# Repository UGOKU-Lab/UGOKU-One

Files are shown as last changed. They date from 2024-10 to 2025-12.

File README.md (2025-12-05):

UGOKU One のハードウェア（KiCad）リポジトリです。

[UGOKU One WEBサイト](https://ugoku-lab.github.io/ugokuone.html)

UGOKU One はモータやセンサを使ったロボットなどのDIY製作物を少しでも手軽に操作することを目的に開発しているオープンソースハードウェアの汎用基板です。
    
- 単四電池ボックス搭載で単四電池4本でDCモーターやRCサーボをの駆動が可能
- Arduinoで開発可能なESP32マイコン搭載(無線通信対応)
- DCモータドライバ（TB67H450FNG）を2個搭載
- 豊富な汎用IOポートでいろんな拡張が可能
- 圧着工具を使用せずにモーターやセンサーの配線が可能

現時点では開発中で動作は未保証です。





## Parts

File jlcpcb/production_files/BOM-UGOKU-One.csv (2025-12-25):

Comment | Designator | Footprint | LCSC | Quantity
0.1μF | C1,C13,C14,C2,C3,C4,C5,C7,C8 | C_0402_1005Metric | C307331 | 9
1.5k | R16,R17,R18,R7 | R_0603_1608Metric | C22843 | 4
10k | R1,R10,R11,R12,R13,R14,R19,R20,R21,R22,R24,R3,R8,R9 | R_0402_1005Metric | C25744 | 14
10μF | C10,C15,C16 | C_0805_2012Metric | C440198 | 3
22.1k | R5 | R_0402_1005Metric | C25768 | 1
22μF | C11,C17,C18,C6,C9 | C_0805_2012Metric | C45783 | 5
47.5k | R6 | R_0402_1005Metric | C25792 | 1
470 | R15,R23 | R_0603_1608Metric | C23179 | 2
470μF | C12 | CP_Elec_6.3x7.7 | C709470 | 1
5.1k | R2,R4 | R_0402_1005Metric | C25905 | 2
AMS1117-3.3 | U3 | SOT-223-3_TabPin2 | C6186 | 1
BMI270 | U4 | XDCR_BMI270 | C2836813 | 1
Battery | BT1 | BAT_2481 | C7174242 | 1
CP2102N-A02-GQFN28 | U1 | IC_CP2102N-A02-GQFN28R | C964632 | 1
Conn_01x02 | J10,J11,J12,J2 | PTS_1.5_2 | C3032345 | 4
Conn_01x10 | J4 | PinSocket_1x10_P2.54mm_Vertical | C2897373 | 1
Conn_02x03_Odd_Even | J3,J8,J9 | PinHeader_2x03_P2.54mm_Vertical_SMD | C3294461 | 3
ESP32-WROOM-32E | U5 | ESP32-WROOM-32E | C701342 | 1
Harting-Conn | J5,J6 | 14110513001000 | C5475480 | 2
K7805M/M78AR05 | U2 | M78AR | C2992391 | 1
LED | L2,L3,L4 | LED_0805_2012Metric_Pad1.15x1.40mm_HandSolder | C84256 | 3
LESD5D5.0CT1G | D1,D2,D3 | D_SOD-523 | C383211 | 3
PWR | L1 | LED_0805_2012Metric_Pad1.15x1.40mm_HandSolder | C434435 | 1
SMBJ6.5A | D7 | D_SMB | C41376096 | 1
SS54 | D4,D5,D6,D8 | D_SMA | C22452 | 4
SS8050 | Q1,Q2 | SOT-23 | C2150 | 2
SSM3K333R | Q3 | SOT-23F | C395454 | 1
SW_DIP_x02 | SW4 | SW_DIP_SPSTx02_Slide_Omron_A6S-210x_W8.9mm_P2.54mm | C6331180 | 1
SW_Push | SW2,SW3 | SW_Push_1P1T_NO_Vertical_Wuerth_434133025816 | C115360 | 2
SW_SPDT | SW1 | SW_SS-12M11G5 | C2879839 | 1
TB67H450FNG_EL | U6,U7 | HSOP-8-1EP_3.9x4.9mm_P1.27mm_EP2.3x2.3mm | C545417 | 2
USB_C_Receptacle_USB2.0_16P | J1 | USB_C_Receptacle_GCT_USB4105-xx-A_16P_TopMnt_Horizontal | C2765186 | 1
Conn_01x04 | J7 | PinHeader_1x04_P2.54mm_Vertical |  | 1

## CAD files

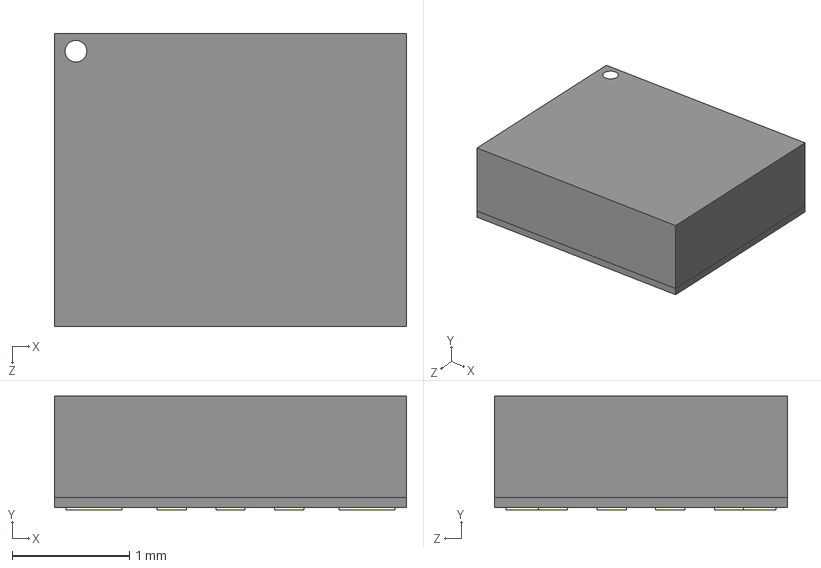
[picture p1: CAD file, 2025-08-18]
3Dmodels/ICM-42605.step
3.00 x 0.97 x 2.50 mm

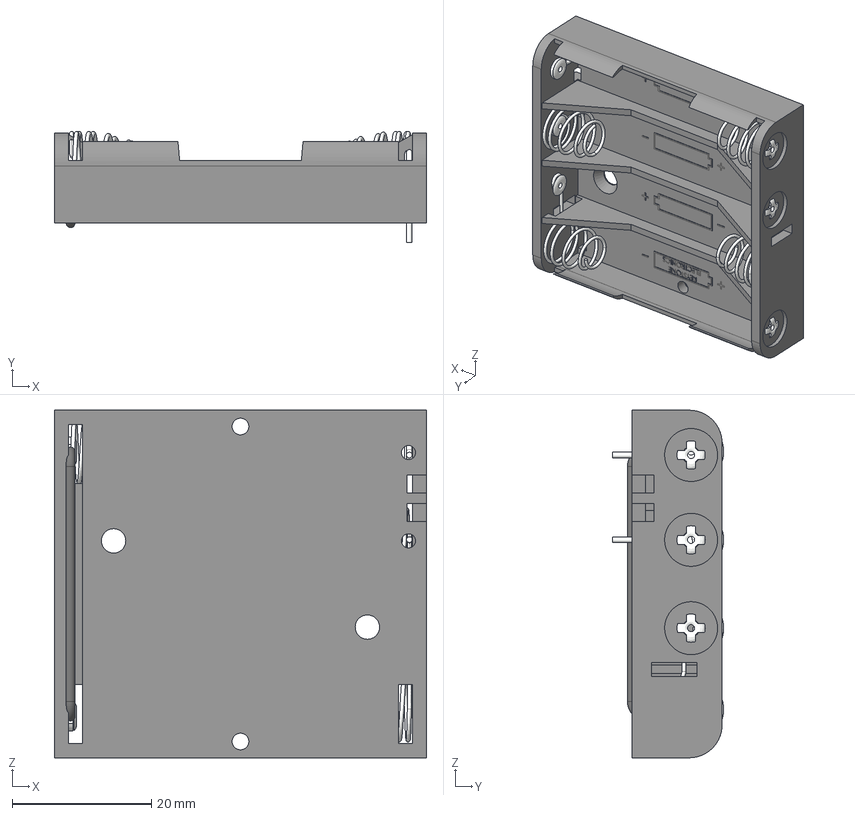
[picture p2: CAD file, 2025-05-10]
3Dmodels/2481_4xAAA_holder.STEP
53.5 x 16.0 x 50.0 mm

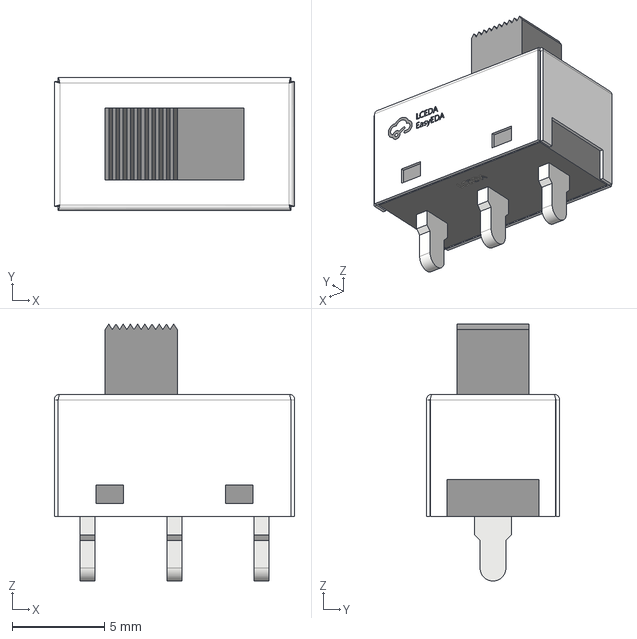
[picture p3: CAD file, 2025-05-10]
3Dmodels/SW_XKB_SS-12M11G5.step
13.0 x 7.20 x 13.9 mm

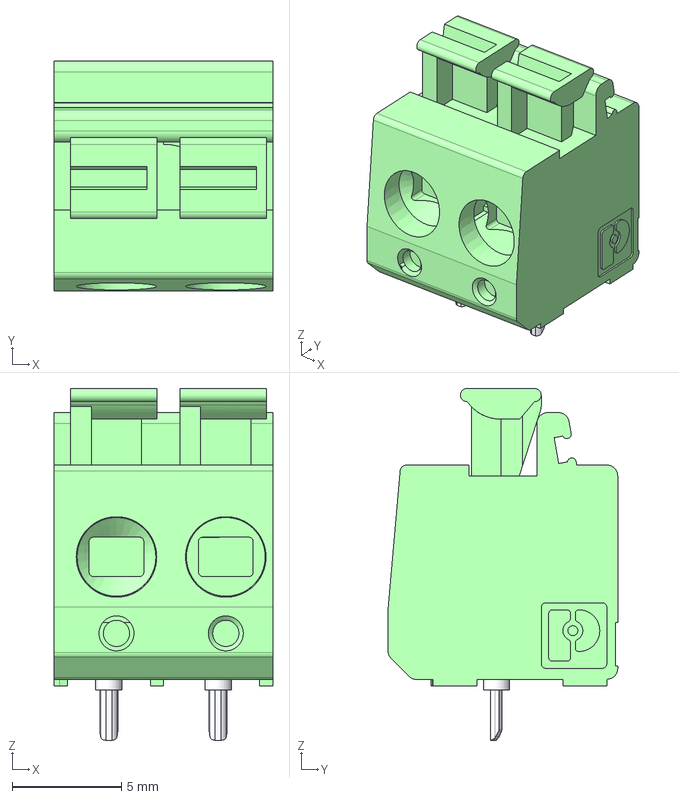
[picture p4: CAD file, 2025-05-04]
3Dmodels/PTS-1-5-2.stp
10.0 x 10.5 x 16.1 mm

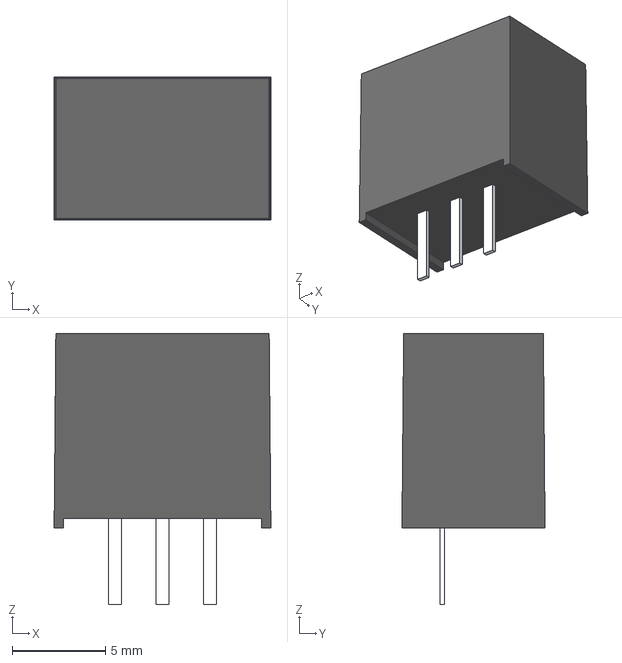
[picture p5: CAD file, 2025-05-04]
3Dmodels/M78AR-1.stp
11.6 x 7.66 x 14.5 mm

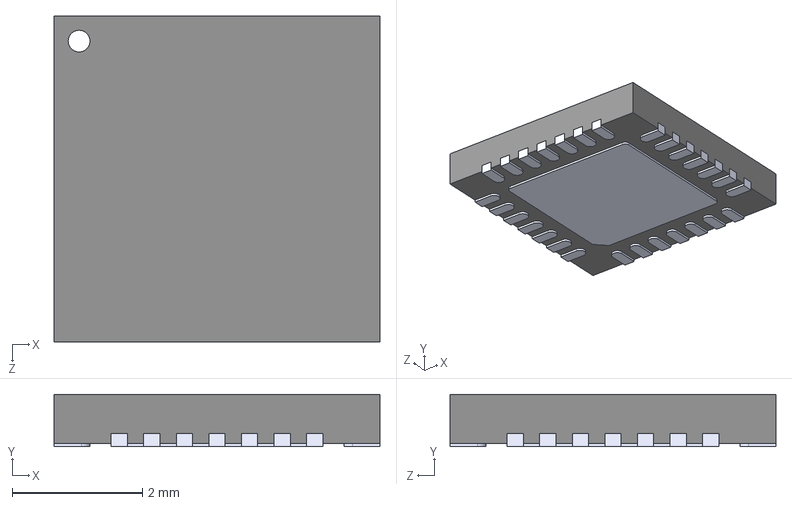
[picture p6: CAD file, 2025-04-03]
3Dmodels/CP2102N-A02-GQFN28R.step
5.00 x 0.8 x 5.00 mm

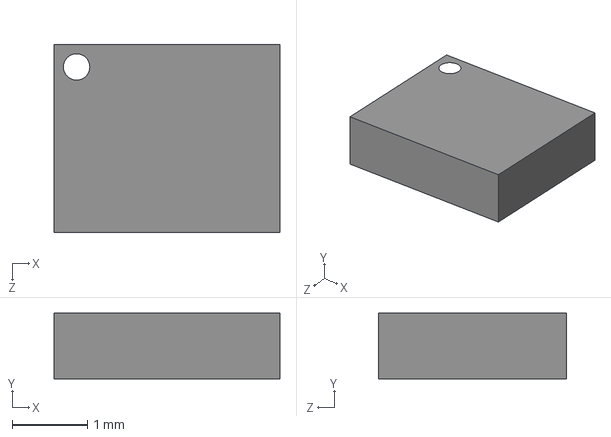
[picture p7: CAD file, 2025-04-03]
3Dmodels/BMI270.step
3.00 x 0.87 x 2.50 mm

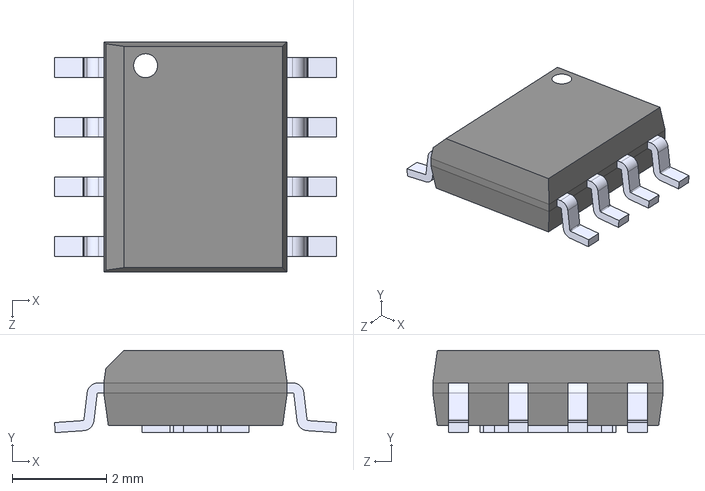
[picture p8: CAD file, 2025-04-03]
3Dmodels/TB67H450FNG.STEP
6.00 x 1.75 x 4.90 mm

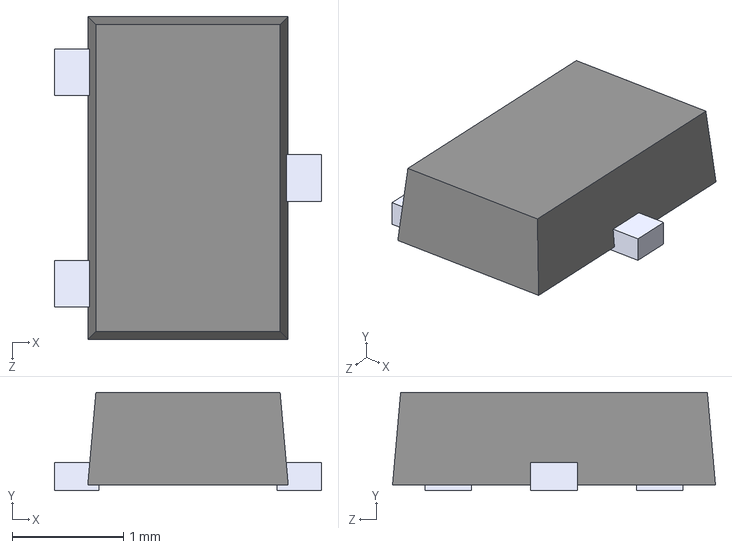
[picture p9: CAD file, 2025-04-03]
3Dmodels/SOT-23F.step
2.40 x 0.88 x 2.90 mm

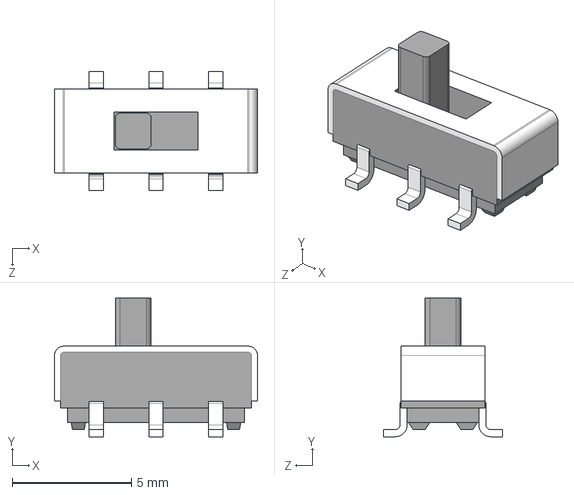
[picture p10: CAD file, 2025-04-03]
3Dmodels/SSSS213202.STEP
8.50 x 5.80 x 5.00 mm

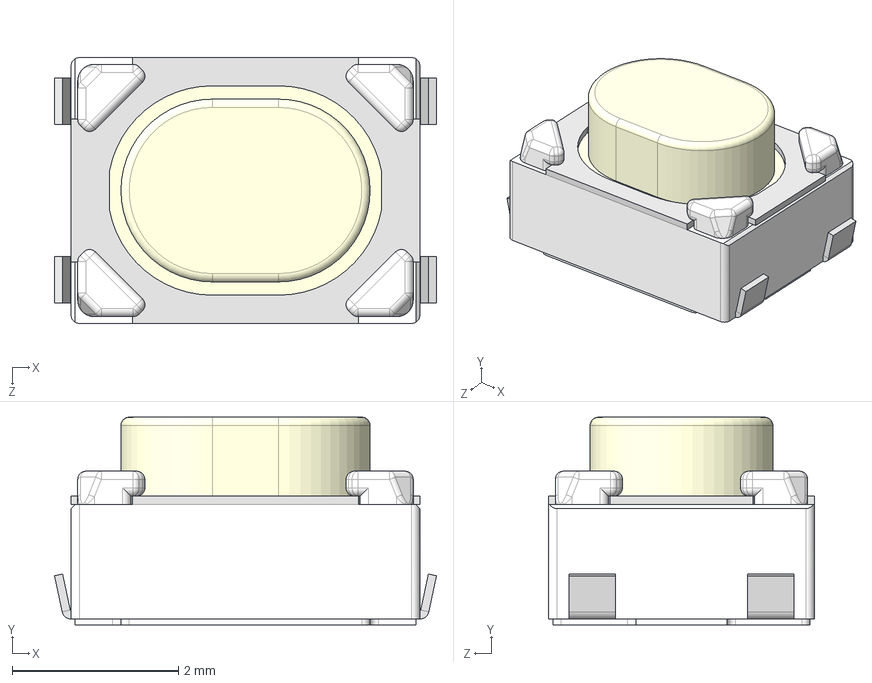
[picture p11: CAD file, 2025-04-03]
3Dmodels/SKRPAB.STEP
4.60 x 2.50 x 3.20 mm

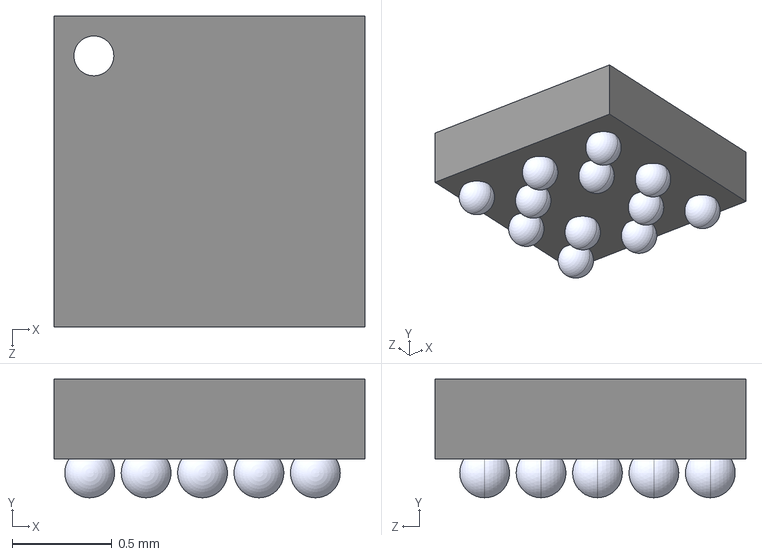
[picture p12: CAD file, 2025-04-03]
3Dmodels/BMM150.STEP
1.56 x 0.595 x 1.56 mm
Body^BMM150
Pin^BMM150 x 12

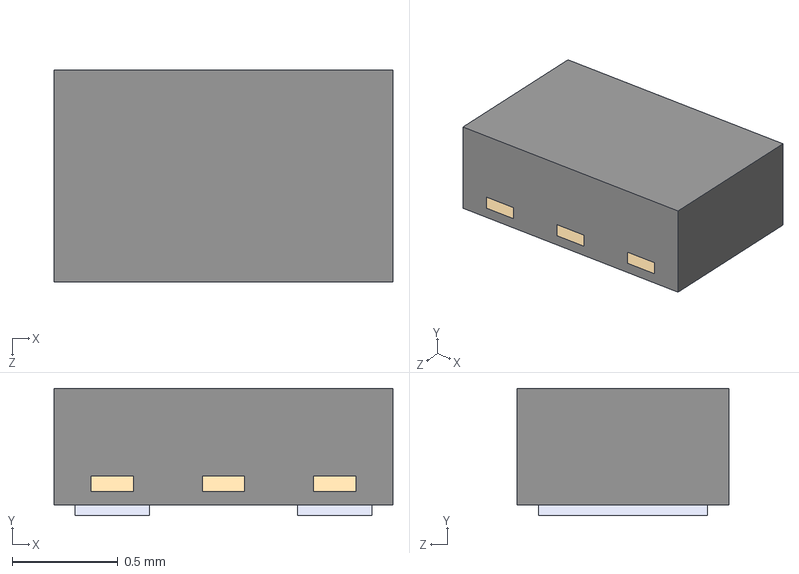
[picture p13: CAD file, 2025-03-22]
3Dmodels/ESDA25P35-1U1M.step
1.60 x 0.6 x 1.00 mm

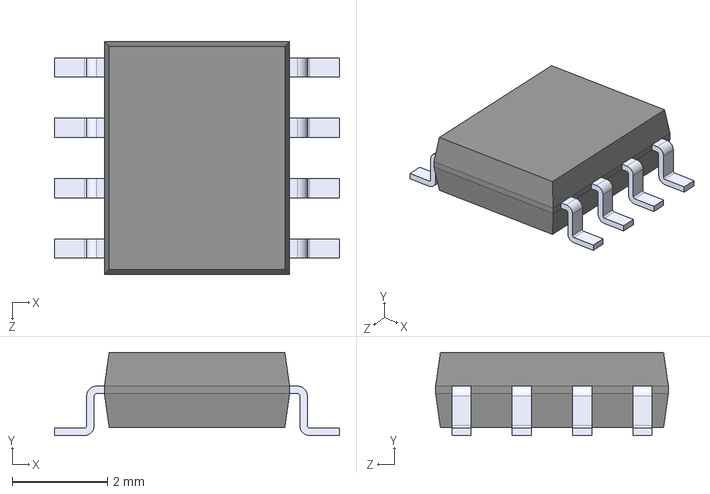
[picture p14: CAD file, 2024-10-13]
3Dmodels/MCP2562-E_SN.step
6.00 x 1.75 x 4.90 mm

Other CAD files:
3Dmodels/TL3301FF160QG.step
3Dmodels/14010213102000.stp
3Dmodels/14110513001000.stp
3Dmodels/14110413001000.stp
3Dmodels/14110213001000.stp
3Dmodels/14110313001000.stp

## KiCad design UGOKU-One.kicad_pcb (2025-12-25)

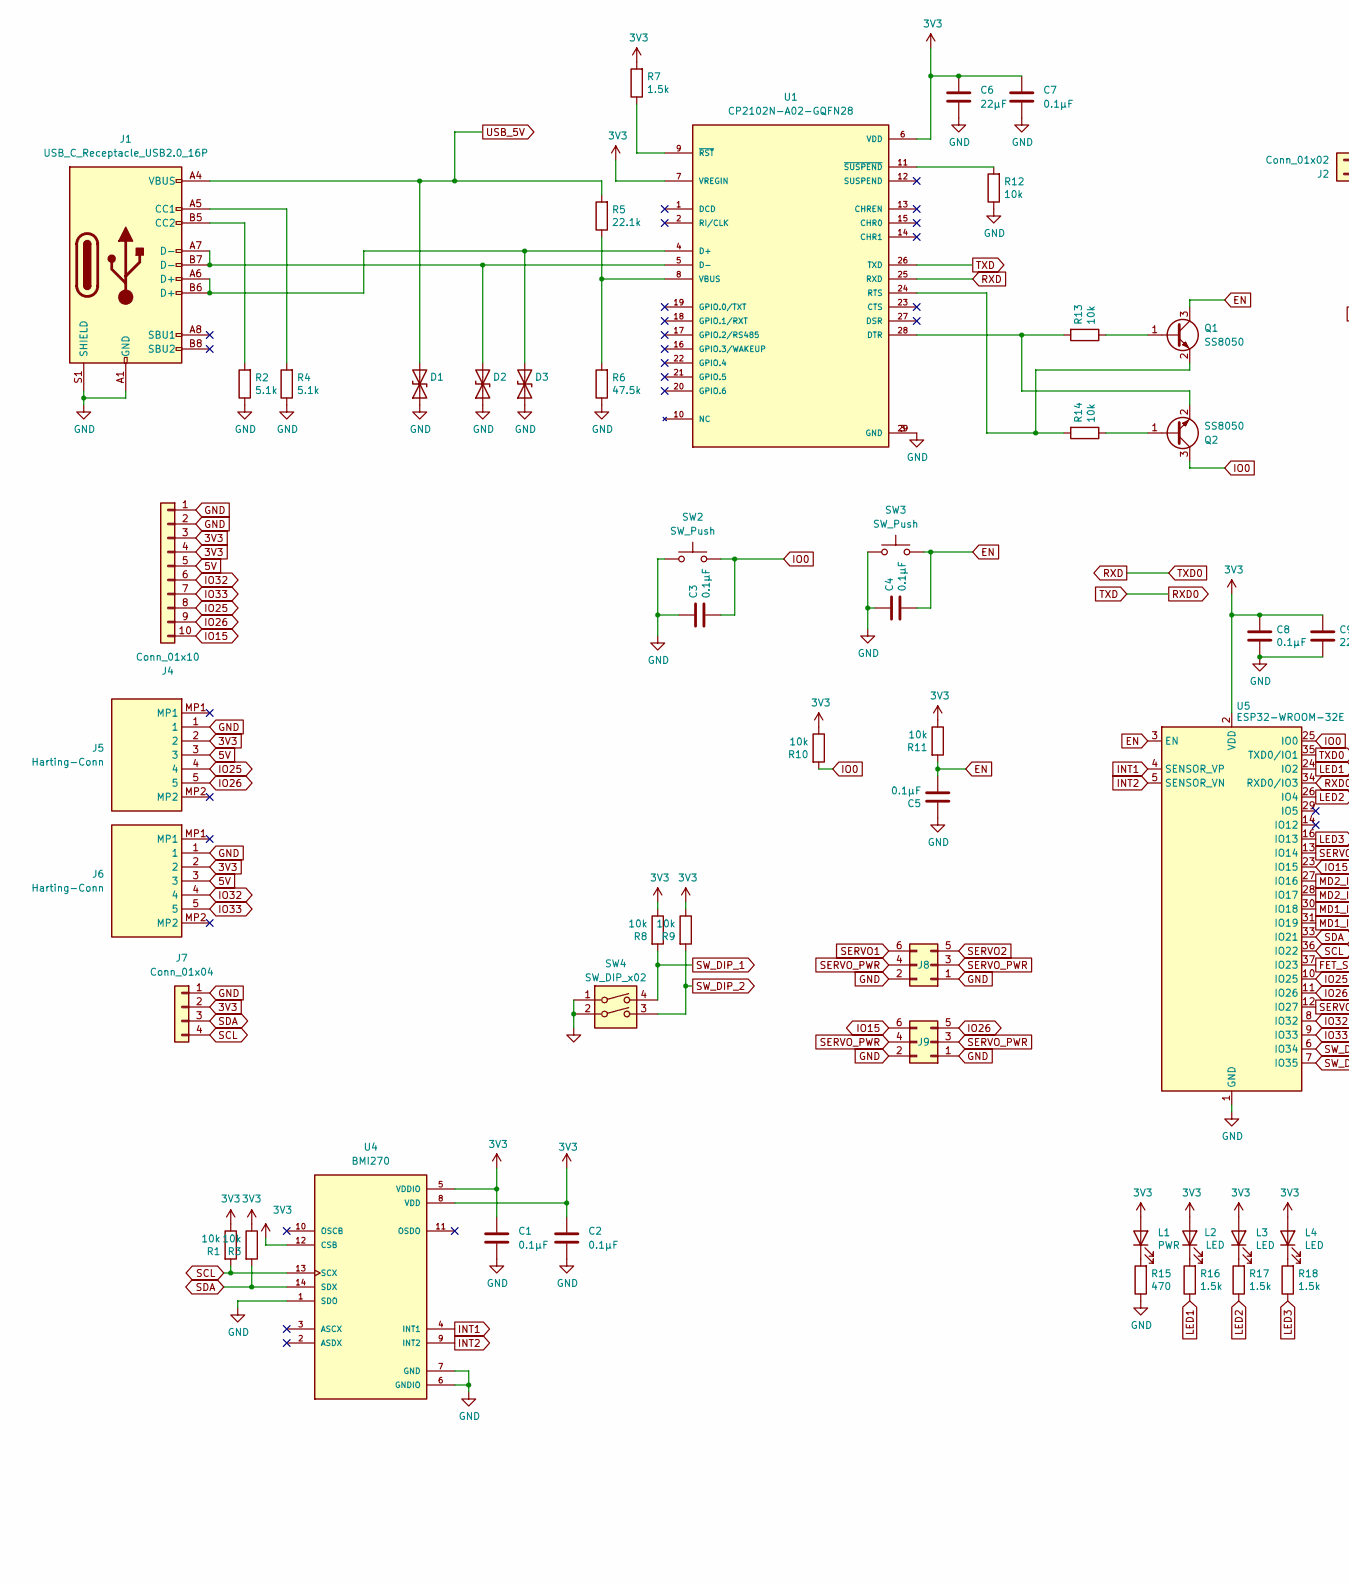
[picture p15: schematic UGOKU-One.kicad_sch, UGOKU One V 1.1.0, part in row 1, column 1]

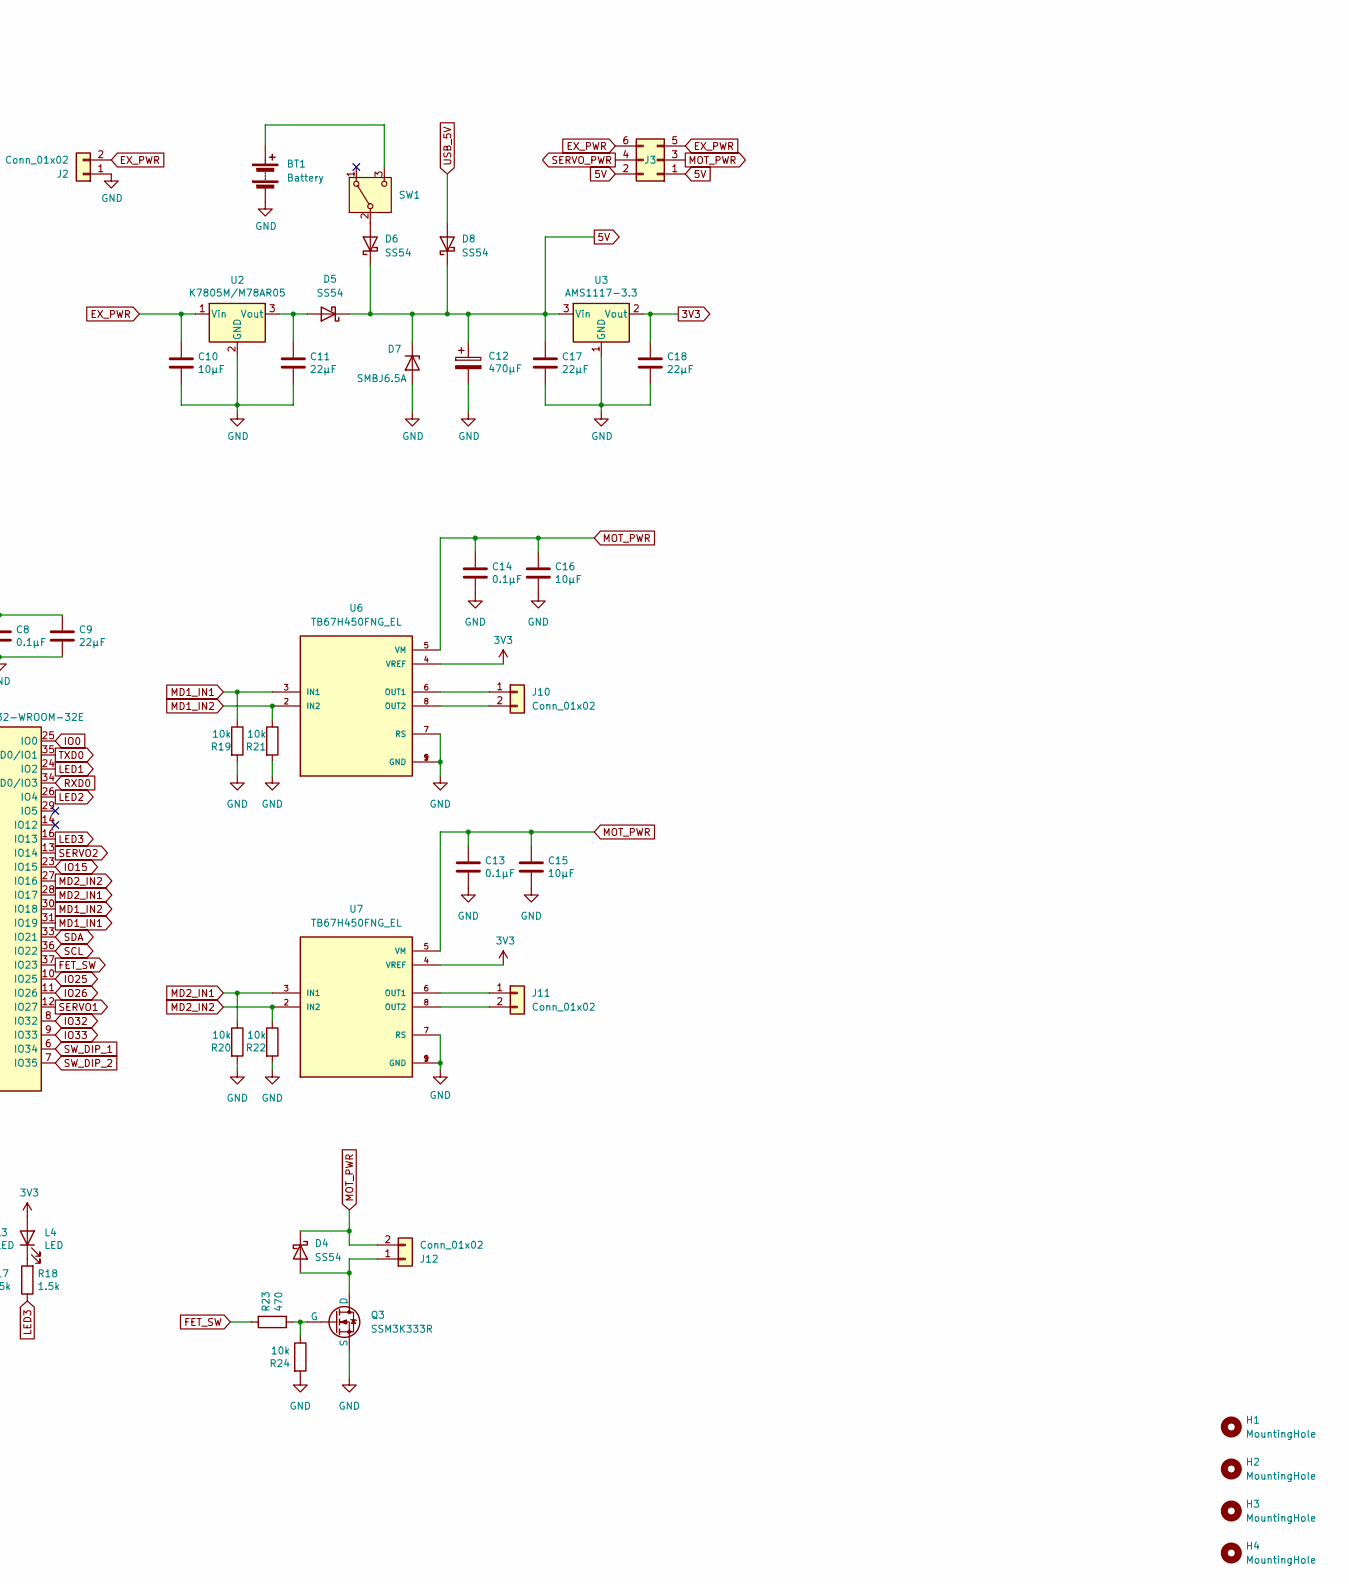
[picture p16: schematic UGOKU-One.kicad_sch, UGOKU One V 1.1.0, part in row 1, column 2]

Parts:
BT1: Battery; BAT_2481
C1, C2, C3, C4, C5, C7, C8, C13, C14: 0.1μF; C_0402_1005Metric
C6, C9, C11, C17, C18: 22μF; C_0805_2012Metric
C10, C15, C16: 10μF; C_0805_2012Metric
C12: 470μF; CP_Elec_6.3x7.7
D1, D2, D3: LESD5D5.0CT1G; D_SOD-523
D4, D5, D6, D8: SS54; D_SMA
D7: SMBJ6.5A; D_SMB
H1, H2, H3, H4: MountingHole; MountingHole_3.2mm_M3
J1: USB_C_Receptacle_USB2.0_16P; USB_C_Receptacle_GCT_USB4105-xx-A_16P_TopMnt_Horizontal
J2, J10, J11, J12: Conn_01x02; PTS_1.5_2
J3, J8, J9: Conn_02x03_Odd_Even; PinHeader_2x03_P2.54mm_Vertical_SMD
J4: Conn_01x10; PinSocket_1x10_P2.54mm_Vertical
J5, J6: Harting-Conn; 14110513001000; Manufacturer_Part_Number 14110513001000; Mouser Part Number 617-14110513001000
J7: Conn_01x04; PinHeader_1x04_P2.54mm_Vertical
L1: PWR; LED_0805_2012Metric_Pad1.15x1.40mm_HandSolder
L2, L3, L4: LED; LED_0805_2012Metric_Pad1.15x1.40mm_HandSolder
Q1, Q2: SS8050; SOT-23
Q3: SSM3K333R; SOT-23F
R1, R3, R8, R9, R10, R11, R12, R13, R14, R19, R20, R21, R22, R24: 10k; R_0402_1005Metric
R2, R4: 5.1k; R_0402_1005Metric
R5: 22.1k; R_0402_1005Metric
R6: 47.5k; R_0402_1005Metric
R7, R16, R17, R18: 1.5k; R_0603_1608Metric
R15, R23: 470; R_0603_1608Metric
SW1: SW_SPDT; SW_SS-12M11G5
SW2, SW3: SW_Push; SW_Push_1P1T_NO_Vertical_Wuerth_434133025816
SW4: SW_DIP_x02; SW_DIP_SPSTx02_Slide_Omron_A6S-210x_W8.9mm_P2.54mm
U1: CP2102N-A02-GQFN28; IC_CP2102N-A02-GQFN28R; PARTREV 1.5
U2: K7805M/M78AR05; M78AR
U3: AMS1117-3.3; SOT-223-3_TabPin2
U4: BMI270; XDCR_BMI270
U5: ESP32-WROOM-32E
U6, U7: TB67H450FNG_EL; HSOP-8-1EP_3.9x4.9mm_P1.27mm_EP2.3x2.3mm; PARTREV 3.0

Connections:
3V3: C1.1, C2.1, C6.1, C7.1, C8.1, C9.1, C18.1, J4.3, J4.4, J5.2, J6.2, J7.2, L1.2 (A), L2.2 (A), L3.2 (A), L4.2 (A), R1.1, R3.1, R7.2, R8.1, R9.1, R10.1, R11.1, U1.6 (VDD), U1.7 (VREGIN), U3.2 (Vout), U4.5 (VDDIO), U4.8 (VDD), U4.12 (CSB), U5.2 (VDD), U6.4 (VREF), U7.4 (VREF)
5V: C12.1, C17.1, D5.1 (K), D6.1 (K), D7.1 (K), D8.1 (K), J3.1, J3.2, J4.5, J5.3, J6.3, U3.3 (Vin)
EN: C4.2, C5.2, Q1.3 (C), R11.2, SW3.2, U5.3 (EN)
EX_PWR: C10.1, J2.2, J3.5, J3.6, U2.1 (Vin)
FET_SW: R23.2, U5.37 (IO23)
GND: BT1.2 (-), C1.2, C2.2, C3.1, C4.1, C5.1, C6.2, C7.2, C8.2, C9.2, C10.2, C11.2, C12.2, C13.2, C14.2, C15.2, C16.2, C17.2, C18.2, D1.1 (A1), D2.1 (A1), D3.1 (A1), D7.2 (A), J1.A1 (GND), J1.A12 (GND), J1.B1 (GND), J1.B12 (GND), J1.S1 (SHIELD), J2.1, J4.1, J4.2, J5.1, J6.1, J7.1, J8.1, J8.2, J9.1, J9.2, Q3.2 (S), R2.1, R4.1, R6.1, R12.1, R15.1, R19.2, R20.2, R21.2, R22.2, R24.2, SW2.1, SW3.1, SW4.1, SW4.2, U1.3 (GND), U1.29 (GND), U2.2 (GND), U3.1 (GND), U4.1 (SDO), U4.6 (GNDIO), U4.7 (GND), U5.1 (GND), U5.15 (GND), U5.38 (GND), U5.39 (GND), U6.1 (GND), U6.7 (RS), U6.9 (GND), U7.1 (GND), U7.7 (RS), U7.9 (GND)
INT1: U4.4 (INT1), U5.4 (SENSOR_VP)
INT2: U4.9 (INT2), U5.5 (SENSOR_VN)
IO0: C3.2, Q2.3 (C), R10.2, SW2.2, U5.25 (IO0)
IO15: J4.10, J9.6, U5.23 (IO15)
IO25: J4.8, J5.4, U5.10 (IO25)
IO26: J4.9, J5.5, J9.5, U5.11 (IO26)
IO32: J4.6, J6.4, U5.8 (IO32)
IO33: J4.7, J6.5, U5.9 (IO33)
LED1: R16.1, U5.24 (IO2)
LED2: R17.1, U5.26 (IO4)
LED3: R18.1, U5.16 (IO13)
MD1_IN1: R19.1, U5.31 (IO19), U6.3 (IN1)
MD1_IN2: R21.1, U5.30 (IO18), U6.2 (IN2)
MD2_IN1: R20.1, U5.28 (IO17), U7.3 (IN1)
MD2_IN2: R22.1, U5.27 (IO16), U7.2 (IN2)
MOT_PWR: C13.1, C14.1, C15.1, C16.1, D4.1 (K), J3.3, J12.2, U6.5 (VM), U7.5 (VM)
unnamed: BT1.1 (+), SW1.3 (C)
unnamed: D2.2 (A2), J1.A7 (D-), J1.B7 (D-), U1.5 (D-)
unnamed: D3.2 (A2), J1.A6 (D+), J1.B6 (D+), U1.4 (D+)
unnamed: D4.2 (A), J12.1, Q3.3 (D)
unnamed: C11.1, D5.2 (A), U2.3 (Vout)
unnamed: D6.2 (A), SW1.2 (B)
unnamed: J1.A5 (CC1), R4.2
unnamed: J1.B5 (CC2), R2.2
unnamed: J10.1, U6.6 (OUT1)
unnamed: J10.2, U6.8 (OUT2)
unnamed: J11.1, U7.6 (OUT1)
unnamed: J11.2, U7.8 (OUT2)
unnamed: L1.1 (K), R15.2
unnamed: L2.1 (K), R16.2
unnamed: L3.1 (K), R17.2
unnamed: L4.1 (K), R18.2
unnamed: Q1.1 (B), R13.1
unnamed: Q1.2 (E), R14.2, U1.24 (RTS)
unnamed: Q2.1 (B), R14.1
unnamed: Q2.2 (E), R13.2, U1.28 (DTR)
unnamed: Q3.1 (G), R23.1, R24.1
unnamed: R5.1, R6.2, U1.8 (VBUS)
unnamed: R7.1, U1.9 (~RST)
unnamed: R12.2, U1.11 (~SUSPEND)
RXD: U1.25 (RXD), U5.35 (TXD0/IO1)
RXD0: U1.26 (TXD), U5.34 (RXD0/IO3)
SCL: J7.4, R1.2, U4.13 (SCX), U5.36 (IO22)
SDA: J7.3, R3.2, U4.14 (SDX), U5.33 (IO21)
SERVO1: J8.6, U5.12 (IO27)
SERVO2: J8.5, U5.13 (IO14)
SERVO_PWR: J3.4, J8.3, J8.4, J9.3, J9.4
SW_DIP_1: R8.2, SW4.4, U5.6 (IO34)
SW_DIP_2: R9.2, SW4.3, U5.7 (IO35)
USB_5V: D1.2 (A2), D8.2 (A), J1.A4 (VBUS), J1.A9 (VBUS), J1.B4 (VBUS), J1.B9 (VBUS), R5.2

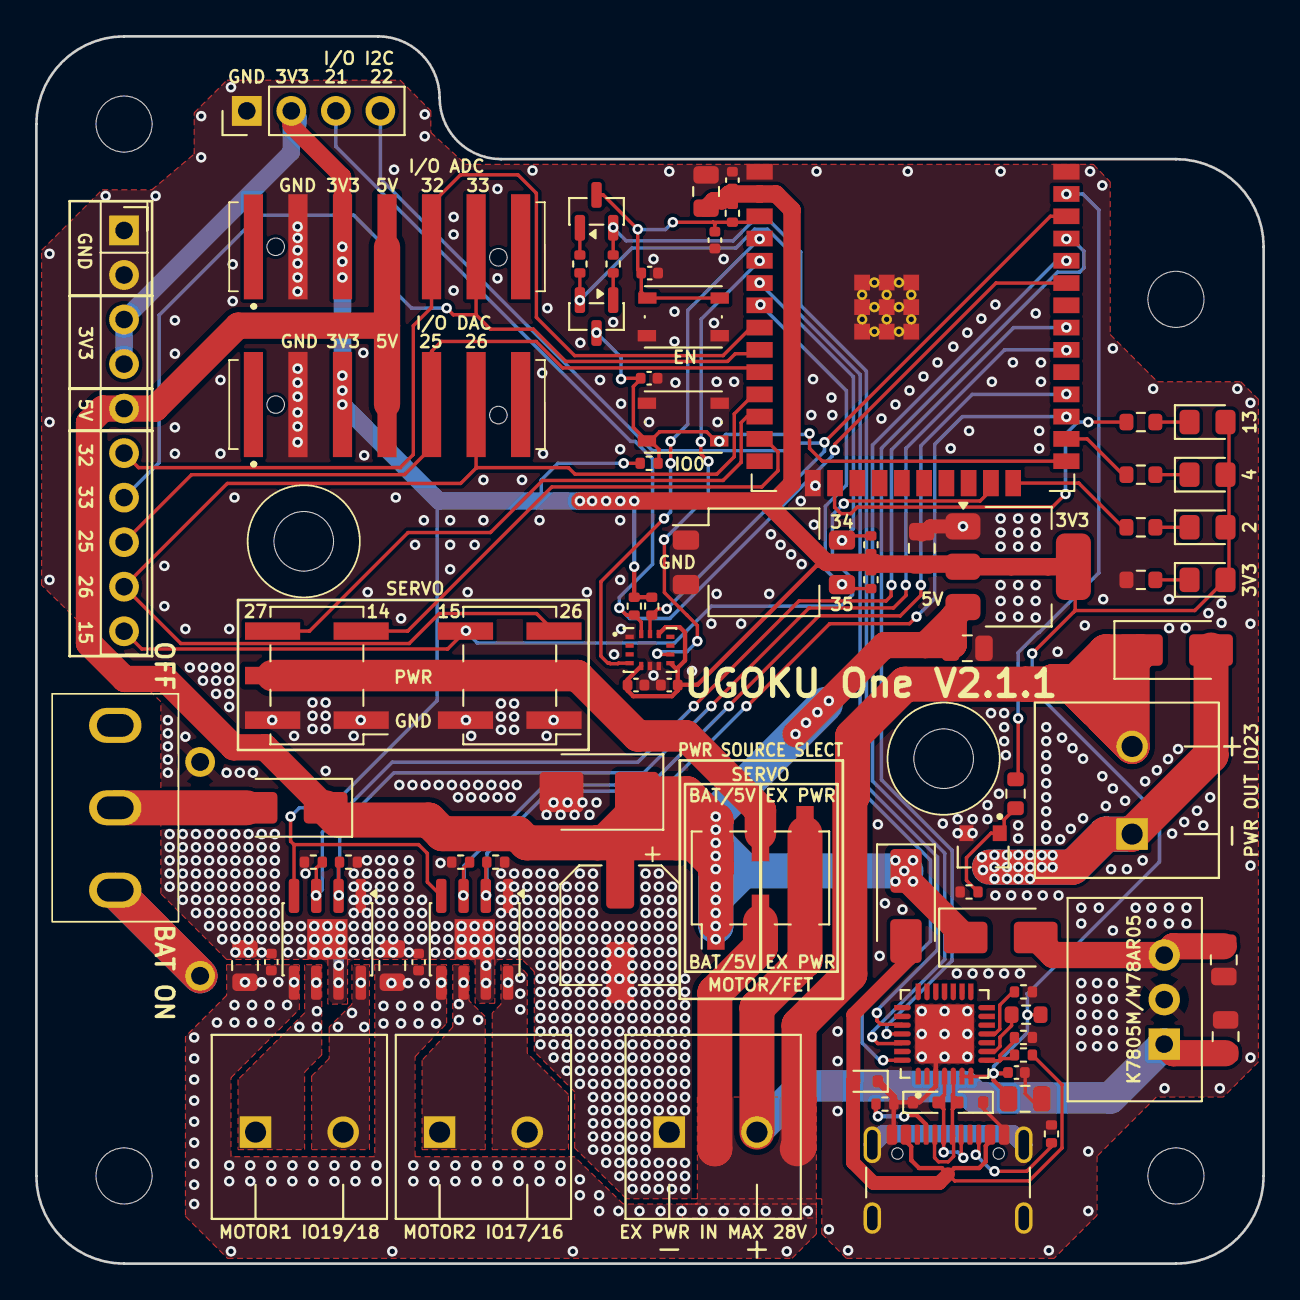
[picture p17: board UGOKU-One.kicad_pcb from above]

Board: 2 copper layers, 70.0 x 70.0 mm, 85 parts (1 on the bottom side), 56 nets.

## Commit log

2024-07-21 Hand over data from previous UGOKU-One (Now UGOKU-Pro)
    [UGOKU-One.kicad_pcb, UGOKU-One.kicad_sch]
2024-07-21 commit iroiro
    [UGOKU-One.kicad_pcb, UGOKU-One.kicad_sch]
2024-10-13 make concept
    [14110213001000.PcbLib, 14110213001000.SchLib, 14110213001000.psm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]
2025-03-17 modify usb, power
    [UGOKU-One.kicad_pcb, UGOKU-One.kicad_sch]
2025-03-22 add PD
    [ESDA25P35-1U1M.step, UGOKU-One.kicad_pcb, UGOKU-One.kicad_sch]
2025-03-28 V1 Rough Layout
    [UGOKU-One.kicad_pcb, UGOKU-One.kicad_sch]
2025-03-30 Add IMU, FET
    [14110213001000.PcbLib, 14110213001000.SchLib, 14110213001000.psm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]
2025-03-31 power layout draft
    [UGOKU-One.kicad_pcb, UGOKU-One.kicad_sch]
2025-03-31 Remove cached KiCad temporary files
2025-04-03 Power:near complete
    [14010213102000.stp, 14110513001000.stp, 2481_4xAAA_holder.STEP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]
2025-04-16 Almost done
    [UGOKU-One.kicad_pcb, UGOKU-One.kicad_sch]
2025-05-04 April-22 order spec
    [UGOKU-One.kicad_pcb, UGOKU-One.kicad_sch]
2025-05-04 update 3dmodel connector color
    [14010213102000.stp, 14110513001000.stp]
2025-05-04 update parts 3dmodel path
    [M78AR-1.stp, PTS-1-5-2.stp, UGOKU-One.kicad_pcb]
2025-05-04 update 3dmodel path
    [UGOKU-One.kicad_pcb]
2025-05-10 update 3dmodels
    [2481_4xAAA_holder.STEP, SW_XKB_SS-12M11G5.step, UGOKU-One.kicad_pcb]
2025-05-16 correct TXRX, regulator pin assign add batt thermal pad
    [UGOKU-One.kicad_pcb, UGOKU-One.kicad_sch]
2025-05-18 align resistor
    [UGOKU-One.kicad_pcb]
2025-06-11 add Motor Drive IN1/2 PIN PullDown, IO0 PIN PullUp
    [UGOKU-One.kicad_pcb, UGOKU-One.kicad_sch]
2025-06-11 Add Title to sch, Update sch pdf
    [UGOKU-One.kicad_sch]
2025-06-14 JLCPCBの要求に対応するため最小viaサイズを0.3/0.5に変更、JLCPCBの要求に対応するためvia-Padクリアランス確保のため地磁気センサBMM150を廃止、スイッチング出力用FETのピン配置を修正
    [UGOKU-One.kicad_pcb, UGOKU-One.kicad_sch]
2025-06-14 IMUの待機電力が微小のため、IMUの電源スイッチを廃止
    [UGOKU-One.kicad_pcb, UGOKU-One.kicad_sch]
2025-08-15 電池ボックスボルトをM2.6に変更 JLCPCB tool 部品表の部品座標、向きを修正
    [UGOKU-One.kicad_pcb]
2025-08-15 CPLファイルの座標と向きを修正、電池ボックスねじ締結指示の画像を追加
    [BOM-UGOKU-One.csv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]
2025-08-18 add part lib
    [ICM-42605.step]
2025-08-23 JLCPCB economy に対応するためIMUをICM-42605に変更
    [UGOKU-One.kicad_pcb]
2025-08-24 ピン配置とコネクタ配置を変更
    [BOM-UGOKU-One.csv, UGOKU-One.kicad_pcb, UGOKU-One.kicad_sch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]
2025-08-31 Update README for ESP32 microcontroller description
2025-10-26 5V電源でアクチュエータを駆動する際の安定性および安全性向上のためにのためにTVSダイオードと電解コンデンサを追加 PCB上に配置（未配線）
    [BOM-UGOKU-One.csv, UGOKU-One.kicad_pcb, UGOKU-One.kicad_sch]
2025-11-22 TVSダイオードをSMBJ6.0に変更
    [BOM-UGOKU-One.csv, UGOKU-One.kicad_pcb, UGOKU-One.kicad_sch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]
2025-12-04 5VラインのコンデンサとTVSダイオードの配線を実施 IMUをBMI270に戻し
    [BOM-UGOKU-One.csv, UGOKU-One.kicad_pcb, UGOKU-One.kicad_sch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]
2025-12-05 配線、ビア、シルクスクリーンの修正
    [UGOKU-One.kicad_pcb]
2025-12-05 ベタGNDとviaを修正
    [UGOKU-One.kicad_pcb, UGOKU-One.kicad_sch]
2025-12-05 ベタGNDを修正
    [UGOKU-One.kicad_pcb]
2025-12-06 MD周りのベタ, viaを修正 BOM,CPLファイルを整備
    [BOM-UGOKU-One.csv, UGOKU-One.kicad_pcb, UGOKU-One.kicad_sch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]
2025-12-06 最新の修正を反映
2025-12-07 ビアの位置を修正
    [UGOKU-One.kicad_pcb]
2025-12-07 製造用CPLファイルの電池ボックスの位置を修正
    [CPL-UGOKU-One.csv]
2025-12-07 コスト削減のため抵抗の種類を統一
    [BOM-UGOKU-One.csv, UGOKU-One.kicad_pcb, UGOKU-One.kicad_sch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]
2025-12-08 抵抗の種類削減
    [UGOKU-One.kicad_pcb, UGOKU-One.kicad_sch]
2025-12-12 アノテーションを更新
    [UGOKU-One.kicad_pcb, UGOKU-One.kicad_sch]
2025-12-12 IOピンのラベル名とアノテーション番号を修正
    [UGOKU-One.kicad_pcb, UGOKU-One.kicad_sch]
2025-12-18 FETの型番を回路図に記載
    [UGOKU-One.kicad_pcb, UGOKU-One.kicad_sch]
2025-12-25 FET熱対策としてFET周りのパターンとviaを修正
    [BOM-UGOKU-One.csv, UGOKU-One.kicad_pcb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]
2026-02-10 FET出力をゲートドライバ駆動に変更、左上のIoConnectorをXAにも対応
